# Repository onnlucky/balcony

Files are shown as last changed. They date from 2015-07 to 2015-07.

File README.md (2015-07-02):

My Balcony Project
----

Getting lots of sun, and very little precipitation, two days without watering,
and my plants on the balcony are dead. Long weekends, never mind holidays,
disastrous. So lets water them automatically.

There is a large bucket of water on the floor.

Hanging at about 2 meters is a plastic balcony plant holder. I selected it for
having only one drain hole. Replaced the hole with a tube outlet. From there
there is tubing to my plants. Plants are at 1 meter height or on the floor.
Once water is in this "bucket" gravity takes care of the rest.

There is a water pump in the bottom bucket, and a hose running to the high
bucket.

I have a 12V 7Amp battery, hooked up to a solar panel. There is a water pump
connected to it via a relays. There is an arduino that can switch the relays.

The arduino is connected to:

1. a relays
2. a moist sensor (in the high bucket)
3. a capacitive water level sensor (in the main bucket)
4. a temerature sensor
5. an esp8266 wifi module
6. a voltage divider sensing battery level

The arduino reports its sensors via the esp8266, and receives the time. Every
morning it will pump at 10:15 until the high bucket is full.

TODO
----

* replace sensor in top bucket (maybe)
* allow setting amount (duration) of water to be pumped, perhaps temperature based etc.
* work on server and interface, to allow more control

Schematic
----

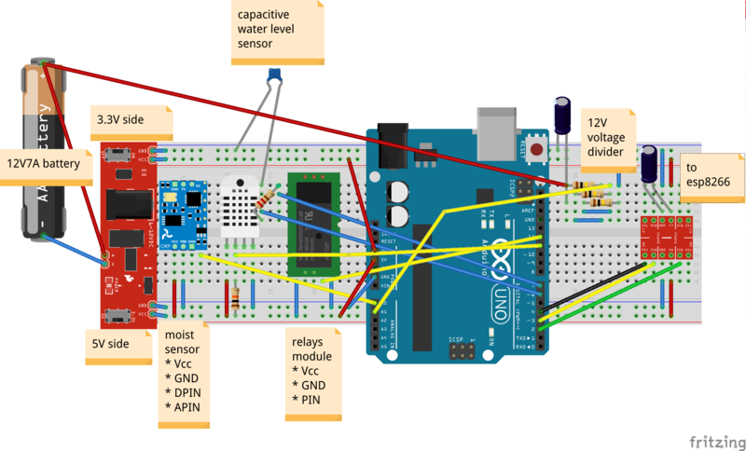
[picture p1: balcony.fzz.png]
fritzing schematic


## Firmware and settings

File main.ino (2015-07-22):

// author: Onne Gorter
// license: CC0 http://creativecommons.org/publicdomain/zero/1.0/

//#define TESTING 1
#include "Time.h"

struct state {
    time_t starttime;
    struct pump {
        int duration;
        bool on;
        time_t next_time;
        time_t last_time;
    } pump;
    struct highbucket {
        time_t last_time;
        int level;
    } highbucket;
    struct mainbucket {
        time_t last_time;
        int level;
    } mainbucket;
    struct temperature {
        time_t last_time;
        float celcius;
        float humidity;
    } temperature;
    struct wifi {
        time_t last_time;
        bool started;
        bool connected;
        uint32_t last_start;
        uint32_t last_connect;
    } wifi;
    struct battery {
        time_t last_time;
        float level;
    } battery;
} state;

#define SSID F("SSID")
#define PASS F("PASS")
#define HOST F("192.168.87.2")
#define PORT 6979
#define GMTOFF (-2 * 60 * 60)

// moist sensor in the high up bucket, used as "full" indicator
#define HIGHBUCKET_LEVEL_PIN A0
#define HIGHBUCKET_ENABLE_PIN 8
#define HIGHBUCKET_LEVEL_REACHED 800

// capacitive water level sensor in the main bucket
#define MAINBUCKET_LEVEL_PIN1 7
#define MAINBUCKET_LEVEL_PIN2 6

// waterpump, pumps from main bucket into the high up bucket
#define PUMP_PIN 12
#define PUMP_MAX_SECONDS 60

// am2302 temperature sensor
#define TEMP_PIN 11

// voltage measurement using voltage devider on battery
// 12V - 100KOhm - 100KOhm + 100KOhm - GND
//                         + pin
#define BATTERY_LEVEL_PIN A1

// esp8266
#define ESP_RX 2
#define ESP_TX 3
#define ESP_RESET 4

#define REV 12

// -- end of config --

#include "capacity.h"
#include "temperature.h"
#include "esp8266.h"
#include <SoftwareSerial.h>
#include <avr/eeprom.h>

#ifdef TESTING
#include <ArduinoUnit.h>
#define TEST_TIME 1435831575UL // 2015-07-02T12:06
#endif

#define NEAR 10

SoftwareSerial esp(ESP_TX, ESP_RX);
ESP8266 wifi(esp, ESP_RESET);
uint8_t packetbuffer[128];

static inline uint8_t checksum(uint32_t from) {
    return (from >> 24) + (from >> 16) + (from >> 8) + from;
}

void setup() {
    esp.begin(9600);
    Serial.begin(9600);

    pinMode(ESP_RESET, INPUT);

    pinMode(PUMP_PIN, OUTPUT);
    digitalWrite(PUMP_PIN, LOW);

    pinMode(13, OUTPUT);
    digitalWrite(13, LOW);

    pinMode(HIGHBUCKET_ENABLE_PIN, OUTPUT);
    digitalWrite(HIGHBUCKET_ENABLE_PIN, LOW);

    uint32_t last_time = eeprom_read_dword((uint32_t*)0);
    uint8_t check = eeprom_read_byte((uint8_t*)4);
    int duration = eeprom_read_word((uint16_t*)5);
    if (checksum(last_time) == check) {
        state.pump.last_time = last_time;
        state.pump.duration = duration;
    }

    Serial.print(F("balcony rev "));
    Serial.print(REV);
    Serial.print(F(" pump.last_time: "));
    char buf[20];
    snprintf(buf, sizeof(buf), "%02d:%02d", hour(state.pump.last_time), minute(state.pump.last_time));
    Serial.println(buf);

    state.wifi.last_start = -30000L;
    state.wifi.last_connect = -30000L;
}

void measure_highbucket_level() {
    digitalWrite(HIGHBUCKET_ENABLE_PIN, HIGH);
    delay(10);
    state.highbucket.level = analogRead(HIGHBUCKET_LEVEL_PIN);
    digitalWrite(HIGHBUCKET_ENABLE_PIN, LOW);
    state.highbucket.last_time = now();
}

void measure_mainbucket_level() {
    state.mainbucket.level = readCapacity2(MAINBUCKET_LEVEL_PIN1, MAINBUCKET_LEVEL_PIN2);
    state.mainbucket.last_time = now();
}

void measure_battery_level() {
    int l = analogRead(BATTERY_LEVEL_PIN);
    float div = (100000.0 + 100000.0 + 100000.0) / 100000.0;
    state.battery.level = l / 1024.0 * 5.0 * div;
    state.battery.last_time = now();
}

#define midnight(T) (((T) / SECS_PER_DAY) * SECS_PER_DAY)
#define hours(H) ((H) * SECS_PER_HOUR)
#define minutes(M) ((M) * SECS_PER_MIN)
void pump_schedule_next(time_t t) {
    state.pump.next_time = midnight(t) + hours(9) + minutes(15);

    if (state.pump.next_time < t) {
        if (!state.pump.last_time || midnight(state.pump.last_time - hours(3)) < midnight(t)) {
            Serial.println(F("pump schedule: now because last_time was not today"));
            state.pump.next_time = t;
        } else {
            Serial.println(F("pump schedule: tomorrow"));
            state.pump.next_time += hours(24);
        }
    }

    // correct any last_time errors
    if (state.pump.next_time < state.pump.last_time) {
        state.pump.last_time = t - 1;
        Serial.print(F("pump schedule: correcting last_time"));
        Serial.println(state.pump.last_time);
    }
}

void pump_off() {
    state.pump.on = false;
    eeprom_write_dword((uint32_t*)0, state.pump.last_time);
    eeprom_write_byte((uint8_t*)4, checksum(state.pump.last_time));
    eeprom_write_word((uint16_t*)5, state.pump.duration);
}

void pump_on(time_t t) {
    measure_highbucket_level();
    measure_mainbucket_level();
    state.pump.on = true;
    state.pump.duration = 0;
    state.pump.last_time = t;
}

void service_pump() {
    uint32_t t = now();
    do {
        if (timeStatus() == timeNotSet) {
            state.pump.on = false;
            break;
        }

        if (state.pump.on) {
            state.pump.duration = t - state.pump.last_time;

            if (state.pump.duration > PUMP_MAX_SECONDS) {
                Serial.println(F("pump off: max time"));
                pump_off();
                break;
            }

            // measurements are taken as fast as possible, when pump is on ...
            if (state.highbucket.level <= HIGHBUCKET_LEVEL_REACHED) {
                Serial.print(F("pump off: highbucket full: "));
                Serial.println(state.highbucket.level);
                pump_off();
                break;
            }

            break;
        }

        if (state.pump.next_time <= state.pump.last_time) {
            pump_schedule_next(t);
            Serial.print(F("pump schedule next: "));
            Serial.println(state.pump.next_time);
            if (state.pump.next_time <= state.pump.last_time) {
                Serial.println(F("OEPS"));
            }
        }

        if (state.pump.next_time <= t) {
            Serial.println(F("pump on: time"));
            pump_on(t);
        }

    } while (false);

    digitalWrite(PUMP_PIN, state.pump.on);
}

void service_temperature() {
    if (state.temperature.last_time + 5 > now()) return;

    float celcius;
    float humidity;
    readAm2302(TEMP_PIN, &celcius, &humidity);

    if (celcius && humidity) {
        state.temperature.celcius = celcius;
        state.temperature.humidity = humidity;
        state.temperature.last_time = now();
    }
}

void service_highbucket() {
    if (!state.pump.on && state.highbucket.last_time + 60 > now()) return;
    measure_highbucket_level();
}

void service_mainbucket() {
    if (state.mainbucket.last_time + 2 > now()) return;
    measure_mainbucket_level();
}

void service_battery() {
    if (state.battery.last_time + 2 > now()) return;
    measure_battery_level();
}

bool start_wifi() {
    if (state.pump.on) return false;

    if ((uint32_t)(millis() - state.wifi.last_start) < 30000UL) return false;
    state.wifi.last_start = millis();

    int s;
    if ((s = wifi.hardwareReset())) {
        Serial.print(F("wifi: reset error "));
        Serial.println(s);
        return false;
    }

    if ((s = wifi.getVersion((char*)packetbuffer, sizeof(packetbuffer)))) {
        Serial.print(F("wifi: version error "));
        Serial.println(s);
        return false;
    }
    Serial.print(F("wifi: esp8266 "));
    Serial.println((const char*)packetbuffer);

    if ((s = wifi.joinAP(SSID, PASS))) {
        Serial.print(F("wifi: join error "));
        Serial.println(s);
        return false;
    }

    if ((s = wifi.getIP((char*)packetbuffer, sizeof(packetbuffer)))) {
        Serial.print(F("wifi: ip error "));
        Serial.println(s);
        return false;
    }
    Serial.print(F("wifi: ip "));
    Serial.println((const char*)packetbuffer);

    state.wifi.started = true;
    return true;
}

bool connect_wifi() {
    if (state.pump.on) return false;

    if ((uint32_t)(millis() - state.wifi.last_connect) < 5000UL) return false;
    state.wifi.last_connect = millis();

    if (!state.wifi.started) {
        if (!start_wifi()) return false;
    }

    int s;
    wifi.putPacketBuffer(packetbuffer, sizeof(packetbuffer));
    if ((s = wifi.tcpOpen(HOST, PORT))) {
        Serial.print(F("wifi: tcp open error "));
        Serial.println(s);
        // restart wifi if tcpOpen timeouts, or if it keeps on failing
        if (s == -1 || (uint32_t)(millis() - state.wifi.last_start) > 30000UL) {
            Serial.println(F("wifi: restarting"));
            state.wifi.started = false;
        }
        return false;
    }

    state.wifi.connected = true;
    return true;
}

void send_data() {
    char buf[300];

    time_t t = now();
    snprintf(buf, sizeof(buf), "%d-%02d-%02dT%02d:%02d:%02d", year(t), month(t), day(t), hour(t), minute(t), second(t));
    Serial.println(buf);

    static const char fmt[] PROGMEM =
        "{id=\"balcony\",r=%d,uptime=%lu,"
        "battery={level=%s,last=%lu},"
        "pump={duration=%d,on=%d,next=%lu,last=%lu},"
        "highbucket={level=%d,last=%lu},"
        "mainbucket={level=%d,last=%lu},"
        "temperature={celcius=%s,humidity=%s,last=%lu}}\n";

    // %f format only works when adding this to gcc: -Wl,-u,vfprintf -lprintf_flt -lm
    char bbuf[14];
    char cbuf[14];
    char hbuf[14];
    dtostrf(state.battery.level, 0, 2, bbuf);
    dtostrf(state.temperature.celcius, 0, 2, cbuf);
    dtostrf(state.temperature.humidity, 0, 2, hbuf);

    int len = snprintf_P(buf, sizeof(buf), fmt,
        REV, now() - state.starttime,
        bbuf, state.battery.last_time + GMTOFF,
        state.pump.duration, state.pump.on, state.pump.next_time + GMTOFF, state.pump.last_time + GMTOFF,
        state.highbucket.level, state.highbucket.last_time + GMTOFF,
        state.mainbucket.level, state.highbucket.last_time + GMTOFF,
        cbuf, hbuf, state.temperature.last_time + GMTOFF);

    if ((unsigned)len >= sizeof(buf)) {
        Serial.print(F("wifi: error buffer too small: "));
        Serial.println(len);
        return;
    }

    Serial.print(buf);

    if (timeStatus() == timeNotSet) return;
    if (!state.wifi.connected) return;

    int s;
    if ((s = wifi.tcpSend((const uint8_t*)buf, len))) {
        Serial.print(F("wifi: error send "));
        Serial.println(s);
        state.wifi.started = false;
        state.wifi.connected = false;
    }
    state.wifi.last_time = now();
}
void process_cmd(const char* buf) {
    if (buf[0] >= '1' && buf[0] <= '4') { // time command
        char* endp = 0;
        time_t t = strtoul(buf, &endp, 10);
        if (endp && endp > buf && t >= 1400000000UL) {
            t -= GMTOFF;
            if (!state.starttime) state.starttime = t;
            setTime(t);
            Serial.print(F("command: set time: "));
            Serial.println(now());
        } else {
            Serial.print(F("command: error setting time: "));
            Serial.println(buf);
        }
    } else if (!strcmp(buf, "pump")) {
        Serial.println(F("command: pump"));
        state.pump.next_time = now();
    } else if (!strcmp(buf, "stop")) {
        Serial.println(F("command: stop"));
        if (state.pump.on) {
            Serial.println(F("pump off: stop received"));
            pump_off();
        }
    } else if (!strcmp(buf, "clear")) {
        Serial.println(F("command: clear"));
        eeprom_write_dword((uint32_t*)0, 0);
        eeprom_write_byte((uint8_t*)4, 0);
        eeprom_write_word((uint16_t*)5, 0);
    } else {
        Serial.print(F("command: error, received: "));
        Serial.println(buf);
    }
}

void service_wifi() {
    if (!state.wifi.connected) {
        if (!connect_wifi()) return;
    }

    int len = wifi.available();
    if (len < 0) {
        Serial.print(F("wifi: receive error "));
        Serial.println(len);
        state.wifi.started = state.wifi.connected = false;
        return;
    }

    if ((unsigned)len >= sizeof(packetbuffer)) {
        Serial.println(F("wifi: error, too much data received"));
        return;
    }

    if (len > 0) {
        char* buf = (char*)wifi.takePacketBuffer();
        // strip buf of whitespace and \n
        for (int i = 0; i < len; i++) if (buf[i] <= 32) buf[i] = 0;
        buf[len] = 0;
        process_cmd((const char*)buf);
        wifi.putPacketBuffer(packetbuffer, sizeof(packetbuffer));
    }
}

void service_statusled() {
    // bit pattern to blink, 8 steps in 2 seconds, 2048 / 8
    uint8_t status = 0x80; // 0b1000_0000

    if (!state.wifi.started) {
        status = 0xFC; // 0b1111_1100
    } else if (!state.wifi.connected) {
        status = 0xCC; // 0b1100_1100
    } else if (timeStatus() == timeNotSet) {
        status = 0xAA; // 0b1010_1010
    }

    int at = (millis() >> 8) & 7;
    digitalWrite(13, (status >> at) & 1);
}

void service_serial() {
    static char buf[100];
    static unsigned at = 0;

    while (Serial.available()) {
        char c = buf[at] = Serial.read();
        if (c <= 32) {
            buf[at] = 0;
            if (at > 0) {
                Serial.write('\n');
                process_cmd(buf);
            }
            at = 0;
        } else {
            Serial.write(c);
            at += 1;
            if (at >= sizeof(buf)) at = 0;
        }
    }
}

void loop() {
#ifndef TESTING
    // first, so measuring sensors etc can use serial buffer
    service_wifi();
#endif

    service_serial();

    service_temperature();
    service_highbucket();
    service_mainbucket();
    service_battery();

#ifdef TESTING
    state.starttime = TEST_TIME;
    setTime(TEST_TIME + (millis() / 50)); // make time go faster
    Test::run();
#endif

    service_pump();
    service_statusled();

    static unsigned long last;
    if ((unsigned long)(millis() - last) > 5000UL) {
        last = millis();
        send_data();
    }
}

// tests

#ifdef TESTING

test(tomorrow) {
    ::state.pump.last_time = TEST_TIME - 1;
    pump_schedule_next(TEST_TIME);

    // must be tomorrow
    assertMore(::state.pump.next_time, midnight(TEST_TIME) + hours(24));
}

test(today) {
    ::state.pump.last_time = TEST_TIME - hours(24);
    pump_schedule_next(TEST_TIME);

    // must be before tomorrow
    assertLess(::state.pump.next_time, midnight(TEST_TIME) + hours(24));
}

test(today_zero) {
    ::state.pump.last_time = 0;
    pump_schedule_next(TEST_TIME);

    // must be before tomorrow
    assertLess(::state.pump.next_time, midnight(TEST_TIME) + hours(24));
}

typedef void(*TrickFn)(time_t dt);

// test the sequence of pumping
class PumpTest : public Test {
public:
    time_t t;
    TrickFn trick;

    PumpTest(const char* name, TrickFn fn=NULL) : Test(name), trick(fn) { }

    void setup() {
        Serial.print(F("setup(): "));
        Serial.println(name);

        t = now();

        memset(&::state, 0, sizeof(::state));
        assertTrue(::state.pump.last_time == 0);
        assertFalse(::state.pump.on);
    }

    void loop() {
        time_t n = now();
        if (trick) trick(n - t);
        do {
            // between 5 - 20 seconds
            if (n >= t + 5 && n <= t + 20) {
                assertTrue(::state.pump.on);
                assertMore(::state.pump.duration, 0);
                assertLessOrEqual(::state.pump.duration, 25);
                assertMore(::state.pump.last_time, 0);
                assertLess(::state.pump.last_time, n);
            }

            // after a minute, little fuzz, as readcapacity with nothing connected takes a while
            if (now() >= t + minutes(1) + 10) {
                assertFalse(::state.pump.on);
                assertMore(::state.pump.duration, 20);
                assertLess(::state.pump.duration, 70);
                assertMore(::state.pump.last_time, 0);
                assertLess(::state.pump.last_time, n);
                assertMoreOrEqual(::state.pump.next_time, midnight(t) + hours(24));
            }

            // after two minutes
            if (now() >= t + minutes(2)) {
                pass();
            }
        } while (false);
    }
};

void trick_highbucket(time_t dt) {
    state.highbucket.level = constrain(HIGHBUCKET_LEVEL_REACHED + (30 - dt) * 10, 500, 1024);
}

PumpTest pumpTest1("pump max seconds");
PumpTest pumpTest2("pump highbucket full", trick_highbucket);

#endif

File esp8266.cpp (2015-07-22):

// author: Feiko Gorter, Onne Gorter
// license: MIT

// comment in to debug the module
//#define DEBUG 1

#include "esp8266.h"
#include <Arduino.h>

// This esp8266 implementation reads from the esp8266 serial, and matches its
// output 4 bytes at the time (uint32_t ESP8266::state), not bothering to
// store the full response in a buffer somewhere. This saves memory and is
// fast. See ESP8266::waitfor

// Also, it can deal with receiving data at any point in while processing
// commands, as long as the user has given a PacketBuffer to the driver.

// It would have been better if the esp8266 wouldn't push +IPD, but instead has
// the other side poll for it. That way the TCP window would shrink to the
// speed at which your program can process data.

// these are the bytes sequences we are looking for as the various reponses
// from the esp.
#define NL_IPD     n(0x2B495044UL) // "+IPD"
#define NL_READY   n(0x64790D0AUL) // "dy\r\n"
#define NL_OK      n(0x4F4B0D0AUL) // "OK\r\n"
#define NL_CHANGE  n(0x6E67650DUL) // "nge\r"
#define NL_FAIL    n(0x494C0D0AUL) // "IL\r\n"
#define NL_ERROR   n(0x4F520D0AUL) // "OR\r\n"
#define NL_CONNECT n(0x43540D0AUL) // "CT\r\n"

// this n function forces to keep these numbers in .text section even when compiled with -Os
static inline uint32_t n(uint32_t n) { return n; }


ESP8266::ESP8266(Stream& esp, int8_t reset_pin) : espconn(&esp), reset_pin(reset_pin), ipdpacket(NULL), ipdlen(0), ipdavailable(0), state(0) { }

int ESP8266::espconnread() {
    int r = espconn->read();
    if (r != -1) return r;

    uint32_t start = millis();
    do {
        int r = espconn->read();
        if (r != -1) return r;
    } while ((uint32_t)(millis() - start) < 100);
    return -1;
}

// just seen +IPD
void ESP8266::receiveIPD() {
    int c = espconnread();
    if (c != ',') return;

    int len = 0;

    while (true) {
        int n = espconnread();
        if (n >= '0' && n <= '9') {
            len = len * 10 + n - '0';
            continue;
        }
        if (n == ':') break;
        return;
    }

    for (int i = 0; i < len; i++) {
        int b = espconnread();
        if (b == -1) return;
        if (!ipdpacket) continue;
        if (ipdavailable >= ipdlen) continue;

        ipdpacket[ipdavailable] = b;
        ipdavailable += 1;
    }

#ifdef DEBUG
    Serial.print(F("+IPD: "));
    Serial.print(len);
    Serial.print(F(" "));
    Serial.println(ipdavailable);
#endif
}

int ESP8266::waitfor(const uint32_t* needles, int nlen, uint32_t timeout, char prompt, char* rec, int reclen, int* at) {
    uint32_t start = millis();
    int recat = 0;

#ifdef DEBUG
    if (timeout) {
        Serial.print(F("waitfor: "));
        Serial.print(nlen);
        Serial.print(F(" "));
        Serial.print(prompt);
        Serial.print(F(" t="));
        Serial.println(timeout);
    }
#endif

    do {
        int alen = espconn->available();
        for (int i = 0; i < alen; i++) {
            uint8_t c = espconn->read();
            state = state << 8 | c;
            if (rec && recat < reclen) rec[recat++] = c;
#ifdef DEBUG
            Serial.write(c);
#endif

            if (state == NL_IPD) receiveIPD();
            if (prompt && (uint8_t)prompt == c) return nlen; // found prompt
            for (int i = 0; i < nlen; i++) {
                if (state == needles[i]) {
                    if (rec && recat < reclen) {
                        rec[recat] = 0;
                        if (at) *at = recat;
                    }
                    return i; // found a needle
                }
            }
        }
    } while ((uint32_t)(millis() - start) < timeout);

    return -1; // timeout
}

void ESP8266::putPacketBuffer(uint8_t* packet, int len) {
    ipdpacket = packet;
    ipdlen = len;
    ipdavailable = 0;
}

int ESP8266::available() {
    if (!ipdavailable) waitfor(NULL, 0, 0);
    return ipdavailable;
}

uint8_t* ESP8266::takePacketBuffer() {
    uint8_t* ret = ipdpacket;
    ipdpacket = NULL;
    ipdlen = 0;
    ipdavailable = 0;

    return ret;
}

int ESP8266::hardwareReset() {
    waitfor(NULL, 0, 0);
    digitalWrite(reset_pin, LOW);
    pinMode(reset_pin, OUTPUT);
    delay(100);
    pinMode(reset_pin, INPUT);
    const uint32_t needles[] = {NL_READY};
    if (waitfor(needles, 1, 2500) < 0) return -1;

#ifndef DEBUG
    espconn->println(F("ATE0"));
    const uint32_t needles2[] = {NL_OK};
    if (waitfor(needles2, 1, 200) < 0) return -1;
#endif

    espconn->println(F("AT+CIPMUX=0"));
    const uint32_t needles3[] = {NL_OK, NL_CHANGE};
    if (waitfor(needles3, 2, 200) < 0) return -1;

    return 0;
}

int ESP8266::reset() {
    waitfor(NULL, 0, 0);
    delay(1000);
    espconn->println(F("AT+RST"));
    const uint32_t needles[] = {NL_READY};
    if (waitfor(needles, 1, 2500) < 0) return -1;

#ifndef DEBUG
    espconn->println(F("ATE0"));
    const uint32_t needles2[] = {NL_OK};
    if (waitfor(needles2, 1, 200) < 0) return -1;
#endif

    espconn->println(F("AT+CIPMUX=0"));
    const uint32_t needles3[] = {NL_OK, NL_CHANGE};
    if (waitfor(needles3, 2, 200) < 0) return -1;

    return 0;
}

int ESP8266::setAPMode() {
    waitfor(NULL, 0, 0);
    espconn->println(F("AT+CWMODE=1"));
    const uint32_t needles[] = {NL_OK, NL_CHANGE};
    return waitfor(needles, 2, 200);
}

int ESP8266::joinAP2() {
    const uint32_t needles[] = {NL_OK, NL_FAIL};
    int res = waitfor(needles, 2, 20000);
    return res <= 0? res : -(res + 1);
}

int ESP8266::joinAP(const char* ssid, const char* pass) {
    if (setAPMode() < 0) return -1;

    waitfor(NULL, 0, 0);
    espconn->print(F("AT+CWJAP=\""));
    espconn->print(ssid);
    espconn->print(F("\",\""));
    espconn->print(pass);
    espconn->println(F("\""));
    return joinAP2();
}

int ESP8266::joinAP(Fstr* ssid, Fstr* pass) {
    if (setAPMode() < 0) return -1;

    waitfor(NULL, 0, 0);
    espconn->print(F("AT+CWJAP=\""));
    espconn->print(ssid);
    espconn->print(F("\",\""));
    espconn->print(pass);
    espconn->println(F("\""));
    return joinAP2();
}

int ESP8266::leaveAP() {
    waitfor(NULL, 0, 0);
    espconn->print(F("AT+CWQAP"));
    const uint32_t needles[] = {NL_OK, NL_ERROR};
    int res = waitfor(needles, 2, 2000);
    return res <= 0? res : -(res + 1);
}

int ESP8266::tcpOpen2() {
    const uint32_t needles[] = {NL_OK, NL_CONNECT, NL_ERROR};
    int res = waitfor(needles, 3, 20000);
    if (res != 0 && res != 1) {
        return res <= 0? res : -(res + 1);
    }

    const uint32_t needles2[] = {NL_OK, NL_CONNECT, NL_ERROR};
    res = waitfor(needles2, 2, 20000);
    if (res != 0 && res != 1) {
        return res <= 0? res : -(res + 1);
    }
    return 0;
}

int ESP8266::tcpOpen(const char* adress, int port) {
    waitfor(NULL, 0, 0);
    espconn->print(F("AT+CIPSTART=\"TCP\",\""));
    espconn->print(adress);
    espconn->print(F("\","));
    espconn->println(port);
    return tcpOpen2();
}
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

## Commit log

2015-06-05 initial checking, adapted http://ed.am/dev/make/arduino-mk
2015-06-05 add moist sensor
2015-06-05 motor on 12, pin 13 flips a lot on resets
    [main.ino]
2015-06-08 Makefile works on linux and older arduino as well
2015-06-14 shorter motor run, but also fixing silent(!) overflow
    [main.ino]
2015-06-19 add esp8266 and support for capacitive water levels
2015-06-21 add temperature sensor
2015-06-21 add global state and time management; pumps at 10:15 in the morning
2015-06-23 add Time.h Time.cpp from arduino, rework structure, make wifi more robust
    [main.ino]
2015-06-25 don't confuse seconds with millis
2015-06-25 fix ESP8266.cpp it likely ignores various +IPD packets
    recv() should be much more reliable, especially when server starts. And
    recv() will report -1 on errors, 0 if no data was received, len otherwise
    look for Linked, instead of OK when connecting a TCP socket
    all recvString, will not consume beyond their targets
    use endsWith, instead of indexOf, much cheaper that way
2015-06-25 simplify wifi and detect read errors
    [main.ino]
2015-06-27 store last pump time in eeprom, with checksum; support more remote commands
2015-06-27 add bucket and main water levels; send data using snprintf_P
2015-06-27 measure capacitance using 8 bits, not 16, so timeouts are short
2015-06-27 service wifi first; capture bucket level when pumping
2015-06-27 update to latest esp8266, using new error reporting
    removed a few bare "..." strings for F("...") strings
    [esp8266.cpp, main.ino]
2015-06-29 fix bad strcmp; add simple server
    [main.ino]
2015-07-02 rename bucket->highbucket; main->mainbucket; remove pump() for statemachine
2015-07-02 add test framework
2015-07-02 add a unit test based on ArduinoUnit
    fix midnight()
    [main.ino]
2015-07-02 allow more tests with tricked timeline
    requires slightly modified arduinounit, to run tests in serial
2015-07-02 add battery level
2015-07-02 adding fritzing schematic
    [balcony.fzz]
2015-07-02 update fritzing graphics
    [balcony.fzz]
2015-07-03 add uptime to reports; sample once per second except for temperature
2015-07-03 try starting wifi at max onces per 30 seconds, connecting at onces per 5 seconds
    only restart wifi if connecting fails for 30 seconds straight
    [main.ino]
2015-07-03 store state.pump.duration in eeprom as well
2015-07-03 blink led 13 to indicate status
2015-07-03 remove mainbucket as pump off condition
2015-07-07 up rev for uptime fix
    [main.ino]
2015-07-07 do server commands; scale graph by days; mark pump_on; scale graph with window
2015-07-08 add low battery and low water warnings
2015-07-22 don't keep highbucket moist sensor engaged, measure less often
